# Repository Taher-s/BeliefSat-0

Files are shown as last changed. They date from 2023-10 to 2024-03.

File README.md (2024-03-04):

# BeliefSat-0

BeliefSat-0 is developed by students of K.J. Somaiya Institute of Technology to widen the reach of Amateur Radio-operators around the globe. The payload is a part of tribute to 100 years of Amateur Radio in India and meant to be in service to the Amateur radio community worldwide. The payload performs UHF to VHF FM Voice Repeating and APRS Digipeating. It has the following amateur radio payloads onboard:

1. Amateur Band UHF to VHF FM voice repeater with 12.5 KHz max bandwidth and 12.5 KHz channel spacing. 67.0 Hz CTCSS tone for uplink. 
1. VHF APRS Digipeater with 71.9 Hz CTCSS tone on the uplink. 

The project was developed by the dedicated student team of our Institute's Student Satellite Program “New Leap Initiative”, led by the expertise of Principal Investigator Dr. Umesh Shinde. 

This project aims to develop and demonstrate the technology utilizing nano-satellite technology to make space tech more accessible to educational and low budget commercial missions, by utilizing inexpensive, off the shelf technologies and easily available materials. 

Working of BeliefSat-0:

1. The satellite was launched through PSLV, this opportunity was presented to us by IN-SPACe (ISRO) as part of their POEM (PSLV Orbital Experimental Module)
1. The satellite is positioned in a 350km orbit with a 8 to 9-degree inclination.
1. Its major function is voice repeating and APRS digipeating for the HAM radio community.
1. In the final stage of the PSLV, the satellite will have a continuous power supply which ensures the satellite's functionality.

### What is it made of? What does it look like? What are its dimensions and mass?

Structure: 

The external structure is constructed using Aluminum 8011.



Mechanical Interface:

|**ID**|**Parameter**|**Unit**|**Specification**|
| :-: | :-: | :-: | :-: |
|Mechanical||||
|1\.|Maximum Estimate Mass of the payload|g|500  |
|2\.|Payload Volume(Excluding Antenna)|mm <sup>3</sup>| 150x118x34 |
|3\. |Payload Volume (Including Antenna)|mm <sup>3</sup>| 150x118x512|
|4\.|Antenna Length (Nagoya NL-770S VHF/UHF High Gain Mobile Antenna)|mm|480|
|5\.|Payload mechanical interface||6x M5 HEX steel bolt|

# How is it Powered?

**Electrical interface:**

Power for the payload is supplied from the launch vehicle to which it is connected by a DB9 connector.

The interface connector details are provided in the table given below:

|**CONNECTOR TYPE**|D-sub 9 Pin Connector|
| :- | :- |
|**On payload**|RECEPTACLE-TYPE (female) (Refer **Images** for pictorial information)|
|**On Launch Vehicle**|PIN-TYPE (male)|
|**Location**|On the side plate, which is situated in the XZ plane (along negative Y axis)|

Only the VCC and the ground pin of the DB9 connector are connected to the vehicle.

Power requirements:

Our payload requires a nominal power supply of 2W and peak power supply of upto 10W

# How does it communicate?

**Transciever Specs**

**VHF**
-**Name :** [DRA818V](http://www.dorji.com/products.php?Keyword=dra818v)
-**Frequency Range :** 134~174 Mhz
-**Channel Space :** 12.5/25 KHz
-**TX Current :** 450/750 mA
-**Temperature :** -20°C ~ +70°C
-**Output Power :** +27/30 dbm
-**Reciever Sensitivity :** -122 dbm (As per datasheet, observed sensititvity yet to be calculated)
 
**UHF**
-**Name :** [DRA818U](http://www.dorji.com/products.php?Keyword=dra818u)
-**Frequency Range :** 400~470 Mhz
-**Channel Space :** 25 KHz
-**TX Current :** 450/750 mA
-**Temperature :** -20°C ~ +70°C
-**Output Power :** +27/30 dbm
-**Reciever Sensitivity :** -122 dbm (As per datasheet, observed sensititvity yet to be calculated) (UHF will only be used for voice repeater uplink)

**Antenna:**

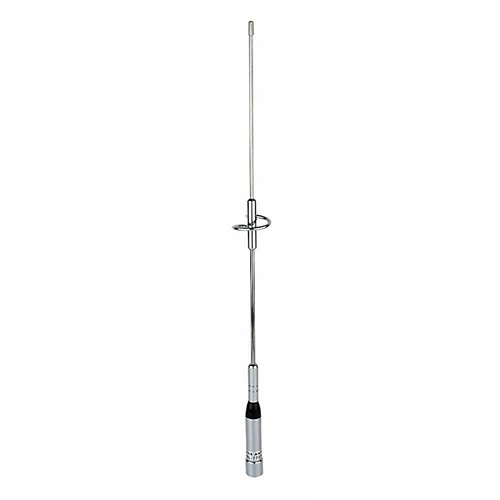
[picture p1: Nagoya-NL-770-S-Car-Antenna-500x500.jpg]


**Nagoya NL-770S VHF/UHF High Gain Mobile Antenna:**

This antenna boasts a unique feature where the satellite's outer cover serves as the grounding mechanism. The carefully engineered radiation pattern, along with impressive gain parameters, ensures strong signal reception and transmission.

What sets the NL-770S apart is its robust construction, making it a reliable choice for various conditions. Its dual-band capabilities cover both VHF and UHF frequencies, enhancing its versatility. The antenna's strategic placement on the satellite, connected via a UHF connector at the top, optimizes signal performance.

**Link Budget:**

- UHF Uplink Budget:

i. Calculation of FSPL() 

= 20x log(D) + 20x log(F) + 20x log (4x pi/c) - G<sub>TX</sub>  - G<sub>RX</sub>               
= 149.9724 dBm

ii. Calculation of Power Received (P<sub>RX</sub>)

= P<sub>TX</sub>+G<sub>TX</sub>-L<sub>TX</sub>-L<sub>FSPL</sub> -L<sub>RX</sub> +G<sub>RX</sub> -</sub> L<sub>M</sub>
= 46.99 + 0 - 0 - 149.9724 - 0 + 0 - 0
= -102.9824 dBm

iii. Link Margin

= P<sub>RX</sub> - RS (Receive Sensitivity)
= (-102.9824 ) - (-122 )
= 19.0176 dBm

- VHF Uplink Budget:

i. Calculation of FSPL

= 20x log(D) + 20x log(F) + 20x log (4x pi/c) - G<sub>TX</sub>  - G<sub>RX</sub>               
= 140.4300 dBm

ii. Calculation of Power Received (P<sub>RX</sub>)

= P<sub>TX</sub>+G<sub>TX</sub>-L<sub>TX</sub>-L<sub>FSPL</sub> -L<sub>RX</sub> +G<sub>RX</sub> -</sub> L<sub>M</sub>
= 46.99 + 0 - 0 - 140.4300 - 0 + 0 - 0
= -93.44 dBm

iii. Link Margin

= P<sub>RX</sub> - RS (Receive Sensitivity)
= (-93.44 ) - (-122 )
= 28.56 dBm

- VHF Downlink Budget:

i. Calculation of FSPL

= 20x log(D) + 20x log(F) + 20x log (4x pi/c) - G<sub>TX</sub>  - G<sub>RX</sub>               
= 140.4300 dBm

ii. Calculation of Power Received (P<sub>RX</sub>)

= P<sub>TX</sub>+G<sub>TX</sub>-L<sub>TX</sub>-L<sub>FSPL</sub> -L<sub>RX</sub> +G<sub>RX</sub> -</sub> L<sub>M</sub>
= 30 + 0 - 0 - 140.4300 - 0 + 0 - 0
= -110.43 dBm

iii. Link Margin 

= P<sub>RX</sub> - RS (Receive Sensitivity)
= (-110.43) - (-121.88 )
= 11.45 dBm

**Operational Modes:**

The operational modes of the payload are:

1. Safe mode (initial mode) : Telemetry once every 30 seconds
1. Digipeater only mode :Telemetry once every 60 seconds and digipeater functionality active
1. Full function mode : Telemetry once every 60 seconds, both digipeater and voice repeater active

In the following description, we have listed three different commands:

1\. Command: !MODE\_CHANGER@<ModeNumber>

Description: This command is used to change the operating mode, and it accepts a ModeNumber parameter that can be set to 0, 1, or 2. Essentially, 0,1, or 2 corresponds to modes 1,2 and 3. 

2\. Command: !VHF\_RX\_FREQ\_CHANGER #<FREQUENCY>

Description: This command is employed for altering the receiving (RX) frequency of a VHF (Very High Frequency) device. You need to specify the desired frequency using the FREQUENCY parameter.

3\.Command:  !VHF\_TX\_FREQ\_CHANGER %<FREQUENCY>

Description: This command allows you to modify the transmitting (TX) frequency of a VHF (Very High Frequency) device. To do this, provide the new frequency as the FREQUENCY parameter.

**Satellite Mode Sequencing and Safety Protocols:**
Upon satellite power-up, it initiates in safe mode, consistently transmitting telemetry every 30 seconds. Following a day of safe mode operations, we issue a command to transition to the digipeater mode. Subsequently, we maintain a one-day duration in digipeater mode before issuing a command to switch to the full mode, enabling both repeater and digipeater functionalities.

The satellite remains in this state, with a daily reset counter uplink command to sustain control. If the reset counter command is not received on any day, it indicates a receiver fault or operational issue. Consequently, the satellite autonomously reverts to safe mode until receiving reactivation instructions, a measure to mitigate potential spurious emissions in cases where the transmitter malfunctions and communication cannot be established.

Hence, a daily connection is imperative, ensuring full communication; otherwise, only telemetry will be transmitted, maintaining the satellite in a state similar to a sputnik.

**What are the different packet types and packet formats?**

**Telemetry Packet**

APRS TELEMETRY FORMAT : The on-air packet telemetry format is as follows:

------>t#51,0,255,255,-12.40,-12.40,xxxxxxBeliefSat<------

51 : LSB of total number of system resets.

0 : MSB of total number of system resets.

255: LSB of total number of resets induced by watchdog

255 : MSB of total number of resets induced by watchdog

-12.40: Temperature sensor 1 reading (Temperature of  Payload )

-12.40: Temperature sensor 2 reading (Temperature of Transreceiver)

xxxxxx : Used as a separation for easier extraction of data in json format

BeliefSat: Name of our Satellite BeliefSat0

References for converting Sensor data into readable format
1. NTC Thermistor: https://robu.in/wp-content/uploads/2016/03/NTC-datasheet.pdf

Refrences for power IC is given below:
1. DC/DC Convertor: https://drive.google.com/drive/folders/0AMwc4gtF42UDUk9PVA

Reference for transreceivers

1. DRA818V :-  [Datasheet](http://www.dorji.com/docs/data/DRA818V.pdf)
1. DRA818U :-  [Datasheet](http://www.dorji.com/docs/data/DRA818U.pdf)

The implementation of APRS packeting system for this project is largely credited to Github user markqvist's LibAPRS repository(https://github.com/markqvist/LibAPRS.git)

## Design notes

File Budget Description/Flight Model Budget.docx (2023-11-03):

To complete the Flight model, following are the expenses towards it:

1. | PCB design and Assembly | Rs. 40000/-
2. | Launch Agreement (Request mail sent to ISRO for concession in launch amount) | Rs. 210000/-
3. | Environmental Testing at SAMEER Kharghar (Request mail sent by PROVOST Sir to DG, SAMEER to reduce the testing cost) | Rs. 332000/-
4. | Traveling for testing and Flight model Submission at SHAR | Rs. 50000/-
| Total | Rs. 632000/-

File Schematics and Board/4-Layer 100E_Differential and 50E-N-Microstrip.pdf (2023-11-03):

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
790 | 50 | 70 | 90 | 110 | 130 | 150 | 170 | 190 | 210 | 230 | 250 | 270 | 290 | 310 | 330 | 350 | 370 | 390 | 410 | 430 | 450 | 470 | 490 | 510 | 530 | 550 | 570 | 590 | 610 | 630 | 650 | 670 | 690 | 710 | 730 | 750 | 770 | 790 | 810 | 830 | 850 | 870 | 890 | 910 | 930 | 950 | 970 | 990 | 1010 | 1030
StackName: 2-Layer | Version: | Revision: | Modification: | Date of Revision: | Editor | Page 2/2
Date: 11-02-2023 | Associated Documents:
Author:
Department:
Site:

www.polarinstruments.com

| Polar Samples | ID/001 | Screened Ident
Polar Samples | SM/001 | Liquid PhotoImageable Mask | 4.000
1 | Polar Samples | FO/002 | Copper Foil | 1.378 | 1, 2, 3
Polar Samples | PP/004 | PrePreg 1651 | 5.906 | 4.200
2 1.378
ISOLA | FR4 | FR4 | 47.244 | 4.300
3 1.378
Polar Samples | PP/004 | PrePreg 1651 | 5.906 | 4.200
4 | Polar Samples | FO/002 | Copper Foil | 1.378 | 4, 5
Polar Samples | SM/001 | Liquid PhotoImageable Mask | 4.000
Polar Samples | ID/001 | Screened Ident ⁶⁴.5669
1 | Coated Microstrip 1B | 1 | 2 | 0 | 9.700 | 0.000 | 49.840 | 50.000 | 10.000 | 0.000
2 | Coated Coplanar Strips With Lower Ground 1B | 1 | 2 | 0 | 8.800 | 0.000 | 50.330 | 50.000 | 10.000 | 9.000
3 | Coated Coplanar Strips With Lower Ground 1B | 1 | 2 | 0 | 8.600 | 0.000 | 50.180 | 50.000 | 10.000 | 8.000
4 | Coated Microstrip 1B | 4 | 3 | 0 | 9.700 | 0.000 | 49.840 | 50.000 | 10.000 | 0.000
5 | Coated Coplanar Strips With Lower Ground 1B | 4 | 3 | 0 | 8.800 | 0.000 | 50.330 | 50.000 | 10.000 | 9.000

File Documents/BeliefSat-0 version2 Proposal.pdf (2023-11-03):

Name of the hosted payload: BeliefSat-0

A. Detailed description of Payload
a) Objective & Introduction
In the rapidly advancing field of space technology, ease of access has frequently posed a challenge, placing restrictions on educational and commercial ventures with limited funding. The proposed project, titled "BeliefSat-0," represents an inspired effort that aims to ignite student curiosity and engagement in the domains of radio-frequency communication and space technology. This project is set to serve as a driving force for STEM education, paving the way for fresh perspectives and involvement.

BeliefSat-0 is developed by students of K.J. Somaiya Institute of Technology to widen the reach of Amateur Radio-operators around the globe. The payload is a part of tribute to 100 years of Amateur Radio in India and meant to be in service to the Amateur radio community worldwide. The payload will perform UHF to VHF FM Voice Repeating and APRS Digipeating. It will have the following amateur radio payloads onboard:

1. Amateur Band UHF to VHF FM voice repeater with 2.5 KHz max bandwidth and 12.5 KHz channel spacing. 67.0 Hz CTCSS tone for uplink.
2. VHF APRS Digipeater with 71.9 Hz CTCSS tone on the uplink.

The ongoing project is in an advanced stage of development by the dedicated student team of our Institute's Student Satellite Program “New Leap Initiative”, led by the expertise of Principal Investigator Dr. Umesh Shinde. At present, significant progress has been made, with the engineering model fully developed and the project now entering the rigorous testing phase. The consistent support from the Institute, serving as the primary funding entity, has played a pivotal role in ensuring the project's continuous advancement, with allocated R&D funds providing vital resources as needed.The team also has got support from the Nanoscience centre of the University of Mumbai for use of cleanrooms, vacuum chambers.

The Principal Investigator has prior experience of creating a Conceptual design of the mission to Jupiter’s moon during “Touch the Jovian Moon: Lander Mission Design Contest” organised by LPSC-ISRO in which they have been winners. The team also has worked on the development of Radiosondes for an Indigenous Upper-Air Sounding System being developed by K.J.S.I.T. in collaboration with DataByte Services and Systems under Make in India initiative. The principal investigator (VU3CDI) is a licensed Amateur Radio Operator. Additionally, the CROWN committee at its core, champions Amateur Radio by sharing essential knowledge and skills. Educational classes equip enthusiasts, including active students, for success in this field. Fostering unity and collaboration among members, especially students, leads to a vibrant exchange of insights and support. This collective effort drives the growth and innovation of the Amateur Radio community. Team has, in the past been successful in developing antennas and software setup for tracking NOAA, METEOR and ISS- ARISS-SSTV downlinks.

b) Payload Objectives :

### 1. Broad Objective:

The proposed project aims to develop and demonstrate the technology utilizing nano-satellite technology to make space-tech more accessible to educational and low budget commercial missions, by utilizing inexpensive, off the shelf technologies and easily available materials.

### 2. Technical Objective:

i. To design the telemetry downlink in such a way that students of different institutes could use inexpensive software-defined radios to receive it with minimal setup, thus giving fuel to curiosity and liking towards STEM education.

ii. To give the ability to the global amateur radio community to use the on-board UHF to VHF FM Voice Repeating and APRS Digipeating for QSOs using inexpensive handy radio setups. (In this case, Baofeng UV-5R being one of the cheapest and most popular handy radios among beginner amateur community, was targeted). This objective has a social and educational objective of getting more students and the general public involved in amateur radio hobby, by giving them an inexpensive access to space-based communication.
iii. To design FSK repeater capabilities in such a way that those could be accessible by off-the-shelf FSK modules available for general IoT projects as well as SDRs like RTL-SDR.
c) Payload specifications

The specifications of the proposed project have been shown in Table below.

1. Specifications of the Payload:
Maximum Estimate Mass of the payload | 500 g
Payload Dimensions (Including Antenna) | Approx. 150x118x512 mm ³
Electrical Interface | On Payload: M24308/23-25F D-Sub Mil Spec Connectors R/A RCP ASSY 9 POS SER 109 From Platform: The expected connection is a male DB9 D-sub connector (9 Pin ) with locking screws on the platform, like a VGA cable
Power requirement from PS4-OP | 28V(raw) for entire duration
Antenna | Nagoya NL-770S VHF/UHF High Gain Mobile Antenna
Participation in integration | Principal Investigator with 2 students will participate.

Post Launch requirements | Tracking and TLE of BeliefSat-0
Command and control station location | KJSIT
Call-sign of the station operator | VU3CDI

Table 1: Specifications of Proposed Payload

2. Payload Description:
BeliefSat-0 is developed by students of K.J. Somaiya Institute of Technology to widen the reach of Amateur Radio-operators around the globe. The payload is a part of tribute to 100 years of Amateur Radio in India and meant to be in service to the Amateur radio community worldwide. The payload will perform UHF to VHF FM Voice Repeating and APRS Digipeating.

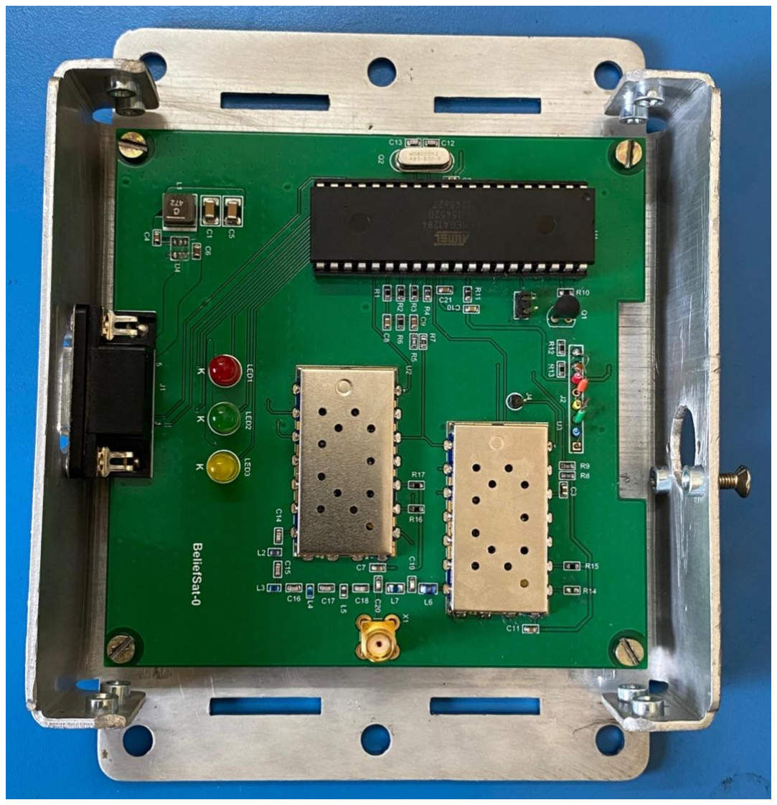
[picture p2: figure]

Fig 2: The engineering model of BeliefSat-0

i. Antenna:

Nagoya NL-770S VHF/UHF High Gain Mobile Antenna:

This antenna boasts a unique feature where the satellite's outer cover serves as the grounding mechanism. The carefully engineered radiation pattern, along with impressive gain parameters, ensures strong signal reception and transmission.

What sets the NL-770S apart is its robust construction, making it a reliable choice for various conditions. Its dual-band capabilities cover both VHF and UHF frequencies, enhancing its versatility. The antenna's strategic placement on the satellite, connected via a UHF connector at the top, optimizes signal performance.

ii) Structure:
Given below is the structural design of our payload with dimensions:

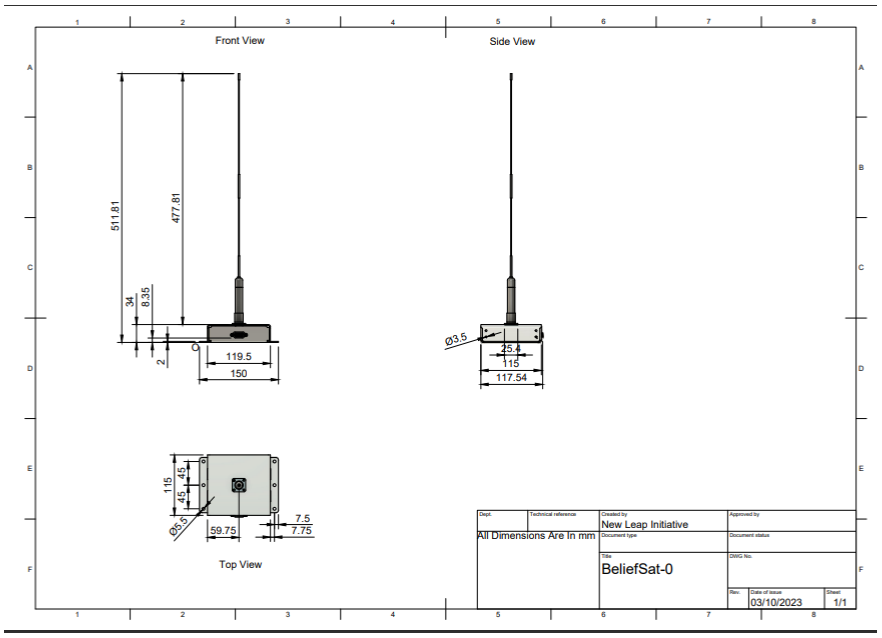
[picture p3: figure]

iii) Electrical Interface:

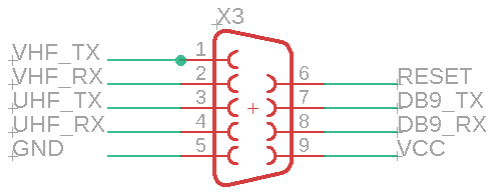
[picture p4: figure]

CONNECTOR TYPE | D-sub 9 Pin Connector
On BeliefSat-0 | RECEPTACLE-TYPE (female)
On Launch Vehicle | PIN-TYPE (male)
iv) | Microcontroller:

ATmega328P is the microcontroller used. The ATmega series is developed by Microchip Technology (formerly Atmel Corporation) is part of the AVR microcontroller family and offers a range of features suitable for various applications, including embedded systems, robotics, and electronics projects. With its advanced capabilities and generous memory, the ATmega328P is well-suited for complex tasks that require efficient processing and control. The selected microcontroller has peripherals like SPI, I2C, Serial, which makes it compatible with most modules in the market. Additionally, it can be easily programmed using Arduino IDE.

v) UHF/VHF Voice Repeater:
An innovative crossband repeater strategy involves pairing VHF and UHF DRA818 transceivers. This dynamic setup enables the seamless rebroadcasting of FM-modulated voice or APRS signals from an input UHF frequency to an output VHF frequency. Emitting at 0.5W output power, the signal remains accessible even to basic walkie talkies. The exceptional input sensitivity of -122dBm ensures quick activation, triggered by the standard 4W output power of prevalent terrestrial amateur radio walkie talkies like the Baofeng UV-5R.

vi) FSK Digipeater:
The primary transceiver also boasts an additional capability to adeptly store-and-forward repeater for concise messages of up to 140 characters. This advanced feature relies on FSK modules, enabling the transceiver to adeptly process and relay brief messages sent its way.

vii) Link Budget:
- UHF Uplink Budget:
i. Calculation of FSPL() = 20x log(D) + 20x log(F) + 20x log (4x pi/c) - GTX - GRX = 149.9724 dBm

ii. Calculation of Power Received (PRX) =PTX+GTX-LTX-LFSPL -LRX +GRX -LM =46.99 + 0 - 0 - 149.9724 - 0 + 0 - 0 = -102.9824 dBm

iii. Link Margin = PRX - RS (Receive Sensitivity)
= (-102.9824 ) - (-122 )
= 19.0176 dBm
- VHF Uplink Budget:
i. Calculation of FSPL = 20x log(D) + 20x log(F) + 20x log (4x pi/c) - GTX - GRX = 140.4300 dBm

ii. Calculation of Power Received (PRX) =PTX+GTX-LTX-LFSPL -LRX +GRX -LM =46.99 + 0 - 0 - 140.4300 - 0 + 0 - 0 = -93.44 dBm iii. Link Margin = PRX - RS (Receive Sensitivity) = (-93.44 ) - (-122 )
= 28.56 dBm
- VHF Downlink Budget:
i. Calculation of FSPL = 20x log(D) + 20x log(F) + 20x log (4x pi/c) - GTX - GRX = 140.4300 dBm

ii. Calculation of Power Received (PRX) = PTX+GTX-LTX-LFSPL -LRX +GRX -LM
=30 + 0 - 0 - 140.4300 - 0 + 0 - 0 = -110.43 dBm

iii. Link Margin = PRX - RS (Receive Sensitivity)
= (-110.43) - (-121.88 )
= 11.45 dBm
c) Specific requirements from POEM (Stability, pointing, orbit type, power etc.) and constraints on payload operation (Electrical, mechanical, environmental)
1. We require 28V(raw) power for the entire duration via male DB9 Connector.
2. Stabilized platform not required
d) Plans for data processing, management and archival
The telemetry and the packets reflected by the digipeater will be received by indigenous ground-stations at K. J. Somaiya Institute of Technology (KJSIT) and will be stored in a local database.
e) Definition of success criteria of the payload

The successful operation of the payload is voice repeating, APRS digipeating functions and changing through different modes of operation using commands sent from the ground station.

B. Development strategy
T0 | Present | 1. Prototype fabrication completed
T0 + 5 weeks | In-house functional testing with firmware | 1. Functional testing of prototype 2. Application for ITU and IARU frequency coordination 3. Designing firmware
T0 + 6 weeks | RF output sensitivity and testing using spectrum analyser | 1. RF output sensitivity and testing using spectrum analyser 2. In-house RF output and Power generation functional testing.
T0 + 7 weeks | Functional testing at Nano-science centre | 1. Preliminary thermal-vacuum bakeout after integration with the satellite at Nanoscience centre University of Mumbai.
T0 + 9 weeks | Flight model fabrication & testing | 1. Fabrication of the flight model (if necessary) 2. Assembly of flight model in clean-room
T0 + 10 weeks | Testing payload using in-house ground station | 1. Testing payload using in-house ground station
T0 + 12 weeks | Qualification Testing | 1. Performing all the required tests like environmental testing, themovac testing, vibration testing and other necessary standard tests.
T0 + 13 weeks | Submission of payload and all the relevant documentation to ISRO | 1. Documentation of code, designs and final test procedures and finalization of required permissions and documents.

C. In case POEM communication capabilities are not required
The team plans to set up its own indigenous ground station at KJ Somaiya Institute of Technology (KJSIT), Sion Mumbai. KJSIT hosts its own Amateur Radio Club – CROWN (Club of Radio Operations and Wireless Networks, VU2CWN) which is a registered club under Wireless Planning and Communication (WPC) wing of Department Of Telecommunication (DOT).
The location of the institute is:
KJ Somaiya Institute of Technology, Sion Mumbai
Somaiya Ayurvihar Complex, Eastern Express Highway, Near Everard Nagar, Sion East, Mumbai, Maharashtra 400022.
CROWN (Club of Radio Operations and Wireless Networks, VU2CWN)
Managed by Dr. Umesh Shinde.
Parameter | Value
Max Bandwidth | 2.5 KHz
Modulation | Frequency Shift Keying (FSK)
Uplink Frequency | 437.525 MHz
Downlink Frequency | 145.525 MHz
Channel Spacing | 12.5 KHz

Data Rates in bps

Telemetry Downlink | 1200
Digipeater Downlink | 1200
Command Uplink | 1200
Digipeater Uplink | 1200

CTCSS tone for uplink

Voice Repeater | 67.0 Hz
APRS Digipeater | 71.9 Hz

D. Description of required post-launch ground operation support.
a. Coordinates of payload.
b. Initial TLEs for the deployed satellite to be provided by the launch service provider.
E. Expected cost for payload realization and source of funding (Intended end use of the experimental payload)
Fully funded by KJ Somaiya Institute of Technology, Sion Mumbai.

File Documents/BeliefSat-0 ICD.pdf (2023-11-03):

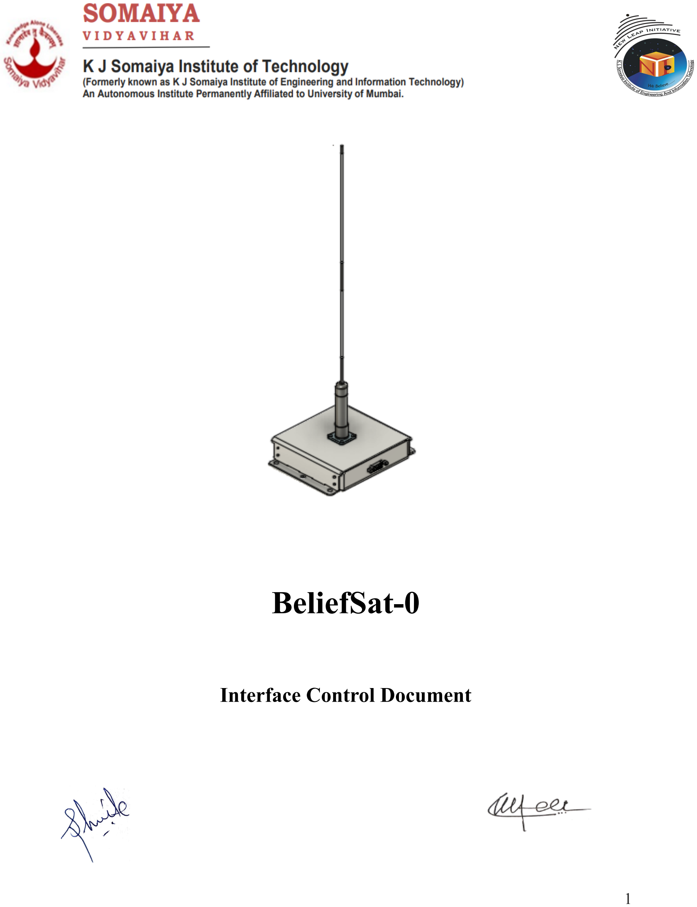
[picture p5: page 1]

# BeliefSat-0

## Interface Control Document

Revised Version | Release Date | Change Record | Effective Pages
1.0 | 25/08/2023 | Proposal Submission | 12
2.0 | 27/09/2023 | Removal of Camera because of tumbling Platform | 12
3.0 | 05/10/2023 | i) Dimensions Changes ii) Addition of Temperature Measure Unit iii) Addition of Short Circuit Protection And Reverse Polarity Protection | 18
4.0 | 18/10/2023 | Change in Fuse | 18
5.0 | 01/11/2023 | Addition of Frequency Band Details in Design Description | 19
6.0 | 02/11/2023 | Typographic mistake in the description of telecommands in Table 1 has been corrected. Frequency Bandwidth changed from 25KHz to 12.5KHz | 19
Revision no. | Approval
Prepared by | Reviewed by | Verified by | Approved by
6.0 | Dhriti Kothari Team Member Student, KJSIT | Sheetal Popat Team Manager Student, KJSIT | Dr. Umesh Shinde Dean, Research Development and Consultancy, KJSIT | Dr. Suresh Ukarande Principal, KJSIT

Sr. no. | CONTENTS | Page No.
1 | Introduction | 5
1.1 | Overview | 5
1.2 | Document Purpose | 5
2 | Payload Overview | 6
2.1 | Design Description | 6
2.2 | General System Requirements | 10
2.3 | Payload Design Parameters | 11
2.4 | Coordinate System | 12
3 | Physical Interfaces | 13
3.1 | Mechanical Interfaces | 13
3.2 | Mass Properties | 14
4 | Electrical Interface | 15
4.1 | Payload - Launch Vehicle Interface | 15

4.2 | The pinouts of DB-9 connector | 15
5 | Appendix A : Overall payload dimensions | 16
6 | Appendix B | 17
7 | Appendix C | 18
8 | References | 19

### 1. Introduction

### 1.1 Overview

BeliefSat-0 is developed by students of K. J. Somaiya Institute of Technology to widen the reach of Amateur Radio-operators around the globe. The payload is a part of tribute to 100 years of Amateur Radio in India and meant to be in service to the Amateur radio community worldwide. The payload will perform UHF to VHF FM Voice Repeating and APRS Digipeating on VHF.

### 1.2 Document Purpose

The interface specifications of Payload are detailed in the document that follows. It provides comprehensive details on the mechanical and electrical interfaces in addition to other important information about the payload.
It will have the following amateur radio payloads onboard:
1. Amateur Band FM voice repeater with 12.5 KHz max bandwidth and 12.5 KHz channel spacing. 67.0 Hz CTCSS tone for uplink.
2. VHF APRS Digipeater with 71.9 Hz CTCSS tone on the uplink.

### 2. Payload Overview

### 2.1 Design Description

Payload is developed by students and the Faculty of K. J. Somaiya Institute of Technology to widen the reach of Amateur Radio-operators around the globe with VHF/UHF FM Voice Repeater and APRS Digipeater.

### 2.1.1 Operational Mode

The operational modes of the payload are:

1. Safe mode (initial mode) : Telemetry once every 30 seconds
2. Digipeater only mode :Telemetry once every 60 seconds and digipeater functionality active
3. Full function mode : Telemetry once every 60 seconds, both digipeater and voice repeater active
Table 1 : Commands for operation mode
Sr. No. | Commands | Description
1. | !MODE_CHANGER@<ModeNumber> | Changes mode between 0,1,2
2. !VHF_RX_FREQ_CHANGER | #<FREQUENCY> | Changes RX frequency of VHF
3. !VHF_TX_FREQ_CHANGER | %<FREQUENCY> | Changes TX frequency of VHF

Note: Detailed command and telemetry formats would be published during frequency coordination

### 2.1.2 Frequency Bands

| VHF Band | UHF Band
Application | Telemetry, Telecommand, Digipeater uplink, Digipeater downlink, Voice Downlink | Voice Uplink
Frequency Range | 144-146 MHz | 435-438 MHz
Desired Central Frequency | 144.2500 MHz | 437.0000 MHz
Bandwidth | 12.5 KHz | 12.5 KHz
Modulation | FM and AFSK over FM | FM
Encoding | APRS over AX.25 using NRZI line coding and AFSK digital Modulation | No Encoding
Transmitting Power | 1W | No Transmit only receive
Area of Operation | Global | Global
Special consideration: | | 3 * VHF Frequency - UHF Frequency | >= 1.5 MHz to prevent feedback loop

### 2.1.3 RF Duplexer Design

Payload has two filter circuits which are HPF (high pass filter) and LPF (low pass filter).
1. High Pass Filter (HPF): This filter allows UHF signals to pass through while blocking VHF signals. By placing an HPF between the DRA818U transceiver and the antenna, it isolates the UHF signals associated with this transceiver from the other.

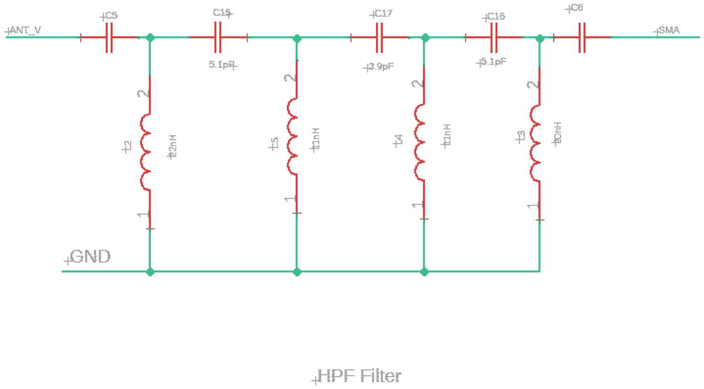
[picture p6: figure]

Fig. 1:High Pass Filter (HPF)
2. Low Pass Filter (LPF): Conversely, an LPF allows VHF signals to pass through while blocking higher-frequency signals. Placing an LPF between the other DRA818 transceiver and the antenna, this helps to isolate the lower-frequency signals associated with that transceiver.

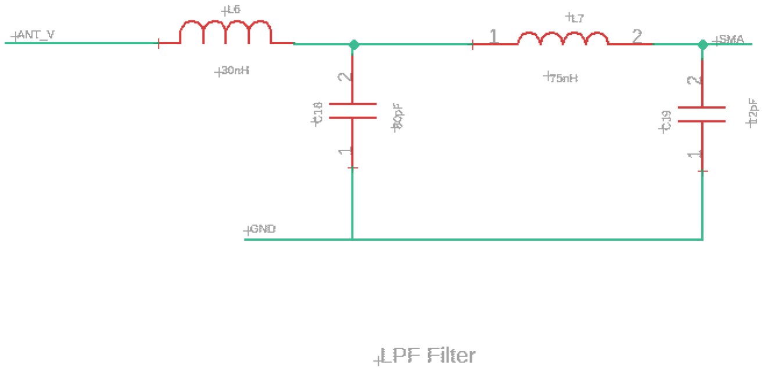
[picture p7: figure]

Fig. 2: Low Pass Filter (LPF)

### 2.1.4 Power Circuit Design:

As per the interface specifications outlined for POEM experimental payloads, the power supplied falls within the range of 24-36 volts in its raw form. To meet these requirements, we have integrated an LM2575S DC to DC buck converter into the system. This converter efficiently transforms the input power into a stable voltage of 3.3 volts while delivering a maximum current output of 2 amperes.

In the implementation of this specific buck converter, two essential protective components have been incorporated. Firstly, a 500mA 125V DC fuse (datasheet included in references) is included to prevent short-circuits effectively. Secondly, a Schottky diode has been employed to ensure reverse polarity protection.
Please refer the provided image below:

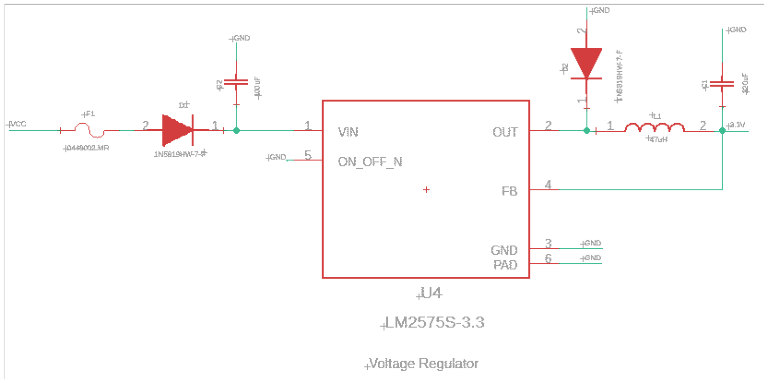
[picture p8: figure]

Fig. 3: Power Circuit Design

### 2.1.5 Temperature measurement unit:

Payload consists of two thermistors (Thermistor 100k NTC) to measure the internal circuit temperature and body temperature. To measure the body temperature one thermistor is fixed to the body using kapton tape and another one fixed on the electronic circuit to measure the circuit temperature.

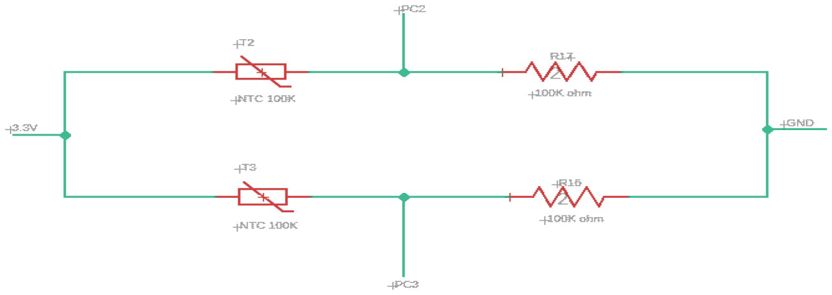
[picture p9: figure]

Fig. 4: Temperature measurement unit

### 2.2 General System Requirements

1. The system includes the necessary electrical and mechanical interfaces with respect to the Launch Vehicle specifications.
2. The payload should be securely connected with the launch vehicle, and is required to receive a continuous power supply within the range of 24V-36V(raw) throughout the entire duration of journey.
3. The payload does not need telemetry and telecommand (TM and TC) requirements from the launch vehicle. Therefore, no communication is required from the platform, except for power supply.

### 2.3 Payload Design Parameters

ID | Parameter | Unit | Specification
| | Mechanical
1. Maximum Estimate Mass of the | payload | g | 500
2. | Payload Volume(Excluding Antenna) | mm ³ | 150x118x34
3. | Payload Volume (Including Antenna) | mm ³ | 150x118x512
4. Antenna Length (Nagoya NL-770S | VHF/UHF High Gain Mobile Antenna) | mm | 480
5. | Payload mechanical interface | | 6x M5 HEX steel bolt

Electrical

6. | Payload electrical interface | - | On Payload: M24308/23-25F D-Sub Mil Spec Connectors R/A RCP ASSY 9 POS SER 109 (Refer Appendix B for pictorial information) From Platform: The expected connection is a male DB9 D-sub connector (9 Pin )
7.. | Power requirement from PS4-OP | - | Nominal: 2 W Peak: 10 W

### 2.4 Coordinate System:

The coordinate system of the payload can be seen in the figure below. The base of the payload is in the XY plane and the antenna is along the Z-axis.

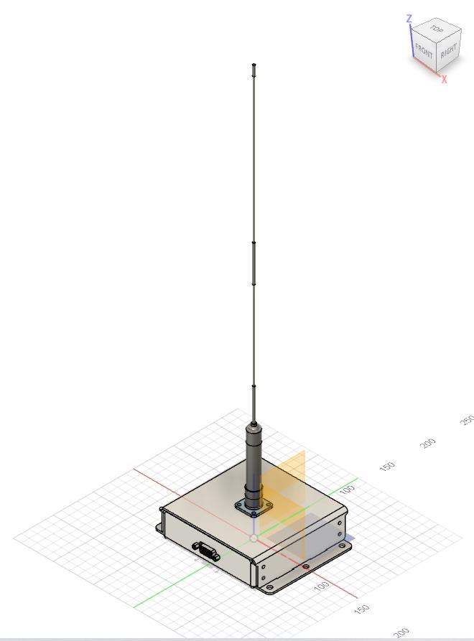
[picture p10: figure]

Fig. 5: Coordinate system

### 3. Physical Interfaces

### 3.1 Mechanical Interfaces

i) The external structure is constructed using Aluminum 8011. The payload is to be mounted on the platform with the help of 6 x M5 HEX steel bolts ( See Fig. 4 ).

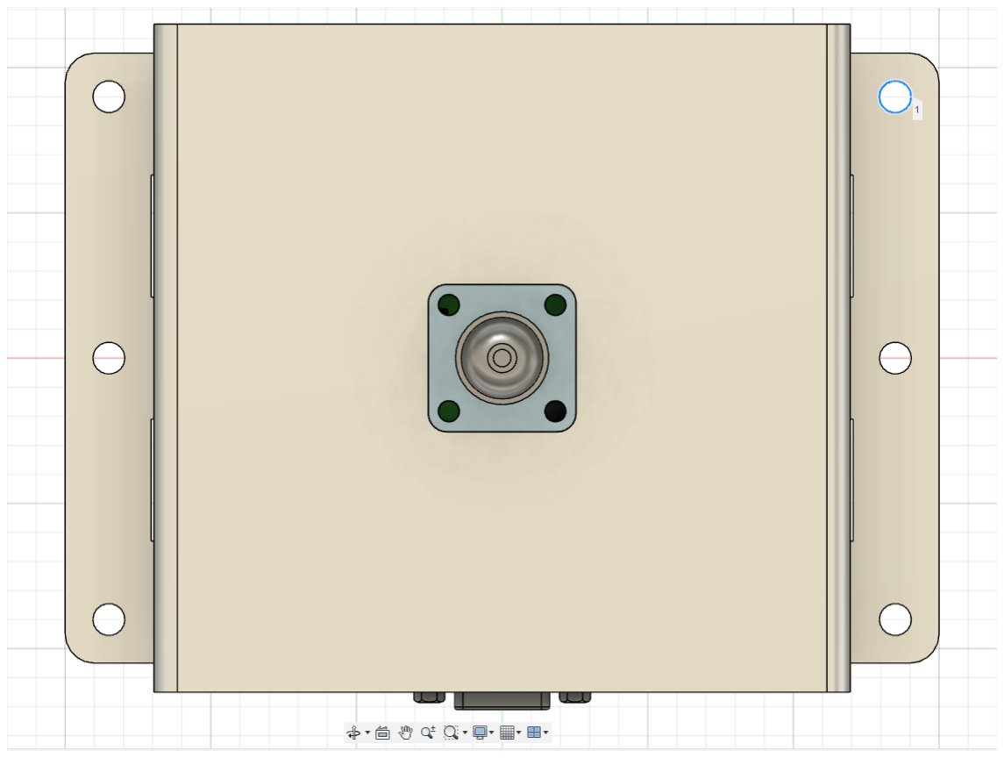
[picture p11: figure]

Fig. 6: 6 M5 holes for mounting
ii) The distance between the center of the mounting hole to the side- wall of the payload is 7.75 mm ( See Fig. 5 ).

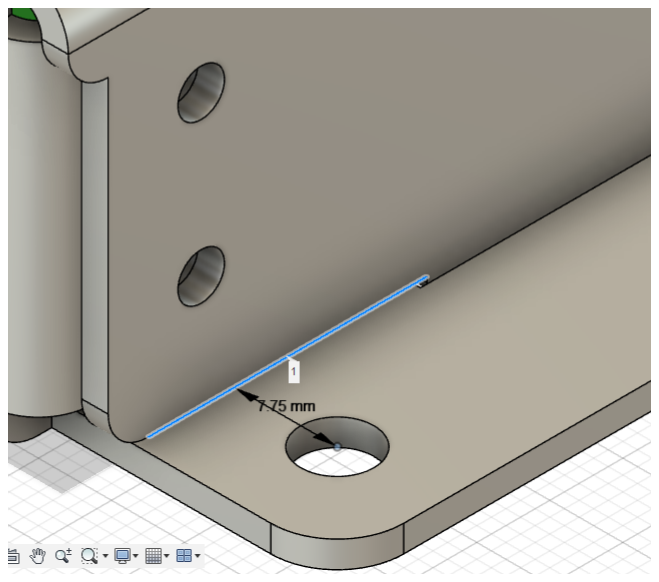
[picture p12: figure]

Fig. 7: Side-wall to mounting hole dimension
iii) Thermal insulating sheet, typically made from material like PEEK, is employed to separate the base from the platform.

### 3.2 Mass properties

Mass, Moment of Inertia and Centre of Mass information is provided in the table below. The values are provided for reference purposes only and it can be used as a baseline input for initial sizing calculations. The following assumptions were taken to generate mass properties:
1. The Moment of Inertia given in the table below is given with respect to the Centre of Mass as well as the Origin position.
Parameter | Value
Mass (g)(Approx.) | 500
Centre of Mass (mm) | X (mm) | -2.324
| Y (mm) | -2.309
| Z (mm) | 27.299
Moment of Inertia (At Centre of Mass) 2 (g mm ) | Ixx | 6 1. 995 x 10
| Iyy | 2.027x 10 6
| Izz | 1. 318 x 10 6
Moment of Inertia (At Origin) 2 (g mm ) | Ixx | 2. 563 x 10 6
| Iyy | 2.595 x 10 6
| Izz | 6 1. 327 x 10

### 4. Electrical Interface

### 4.1 Payload - Launch Vehicle Interface

The interface connector details are provided in the table given below:

CONNECTOR TYPE | D-sub 9 Pin Connector
On payload | RECEPTACLE-TYPE (female) (Refer Appendix B for pictorial information)
On Launch Vehicle | PIN-TYPE (male)
Location | On the side plate, which is situated in the XZ plane (along negative Y axis)

### 4.2. The pinouts of DB-9 connector are given in the table below (we require only VCC

and GND from the platform):

Pin Number | Name | Description
1 | TX_VHF | NC
2 | RX_VHF | NC
3 | TX_UHF | NC
4 | RX_UHF | NC
5 | GND | Ground
6 | RESET_DB9 | NC
7 | TX_DB9 | NC
8 | RX_DB9 | NC
9 | VCC | Power Supply
The schematic diagram of the DB -9 connector is given in Appendix C (Electrical Interface Schematics).

### 5. Appendix A: Overall dimensions of Payload

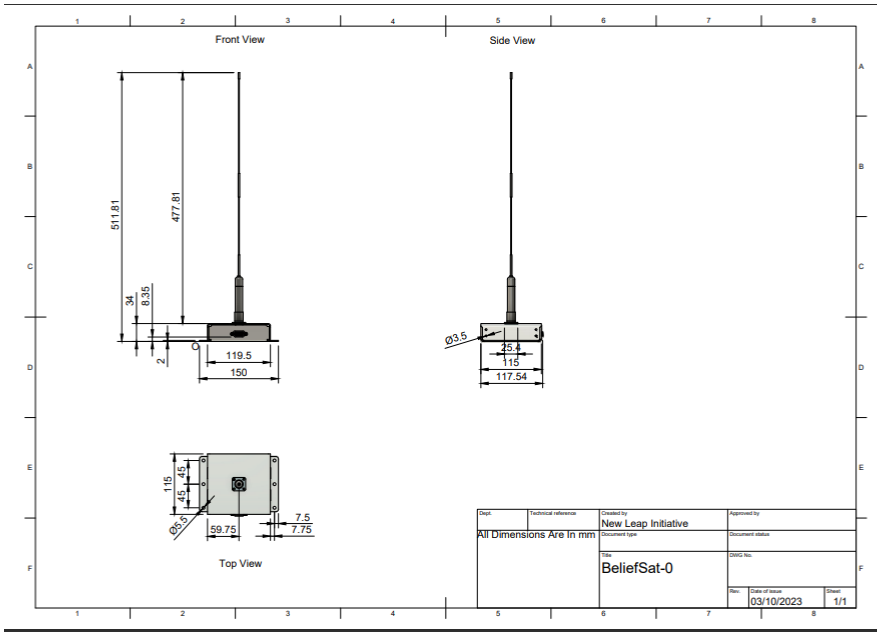
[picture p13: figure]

Fig. 8: Dimensions of Payload (in mm)

### 6. Appendix B: Overall dimensions of Connector Used For Electrical Interface

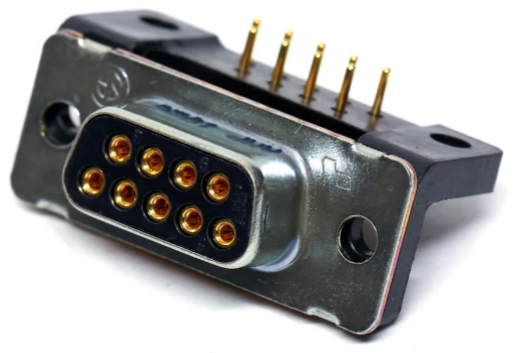
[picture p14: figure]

Fig. 9: M24308/23-25F D-Sub Mil Spec Connectors

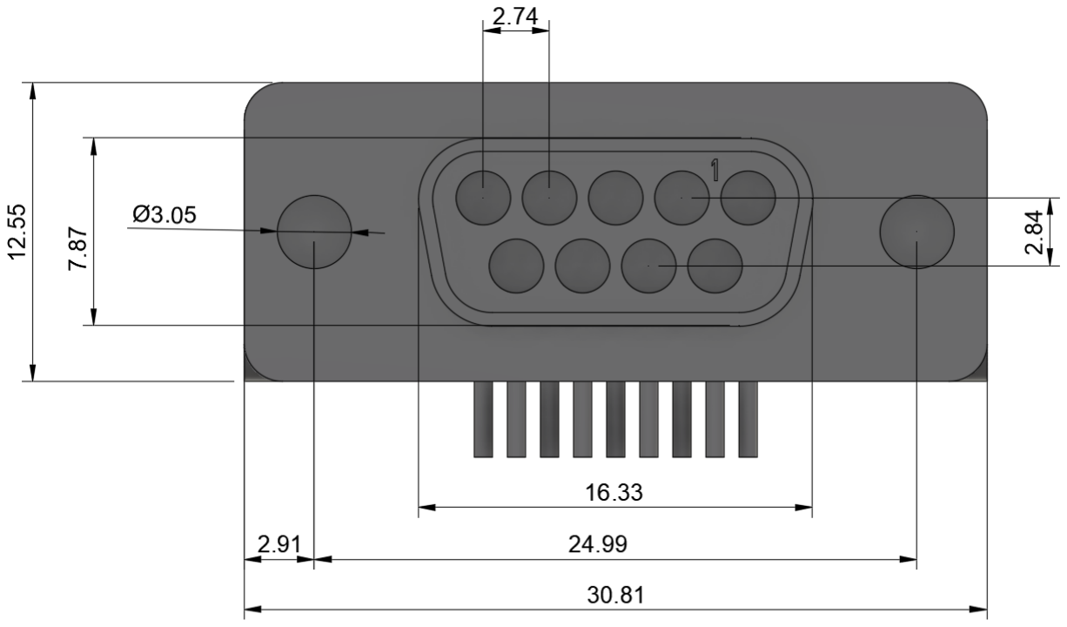
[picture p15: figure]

Fig. 10: DB9 Connector Dimensions
The base of the DB9 connector is positioned at a distance of 10.24 mm above the payload base, while the screws are situated 14.19 mm above the payload base.

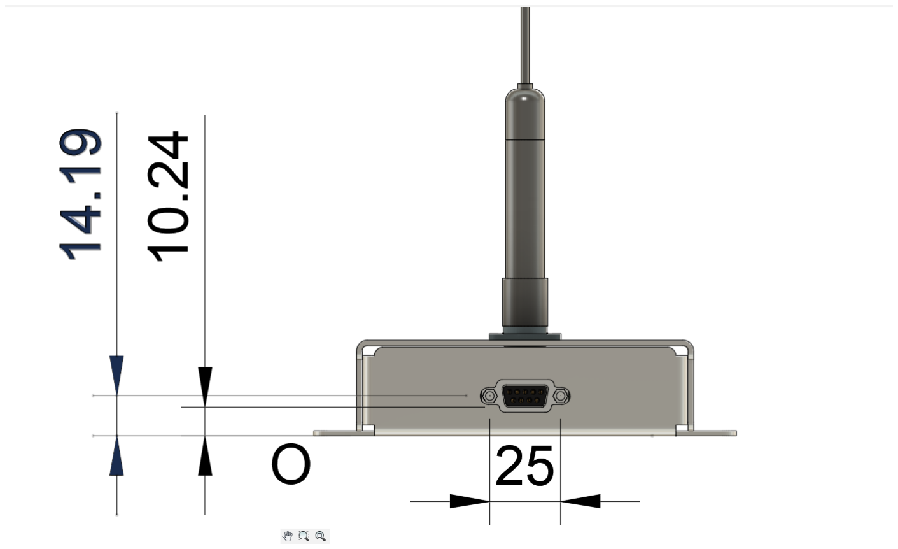
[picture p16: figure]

Fig. 11: DB9 Connector Location on Package

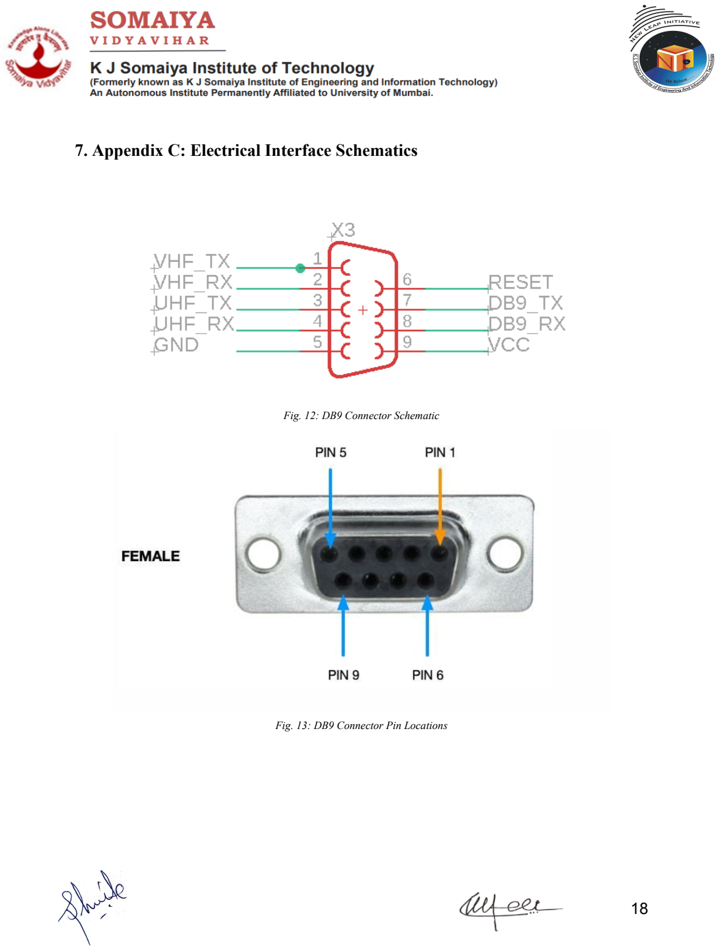
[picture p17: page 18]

### 7. Appendix C: Electrical Interface Schematics

Fig. 12: DB9 Connector Schematic

Fig. 13: DB9 Connector Pin Locations

### 8. References :

i. Microcontroller datasheet (Atmega328P-PU) https://www.mouser.in/datasheet/2/268/ATmega48A_PA_88A_PA_168A_PA_328_P_DS_DS40 002061B-3050139.pdf (https://www.mouser.in/datasheet/2/268/ATmega48A_PA_88A_PA_168A_PA_328_P_DS_DS40002061B-3050139.pdf)

ii. DC to DC Buck Converter (LM2575S IC REG BUCK 3.3V 2A TO263-5L) https://mm.digikey.com/Volume0/opasdata/d220001/medias/docus/5011/LM2575-LM2575HV.p df (https://mm.digikey.com/Volume0/opasdata/d220001/medias/docus/5011/LM2575-LM2575HV.pdf)

iii. Fuse (LITTELFUSE 0451.500MRL) https://drive.google.com/drive/folders/1YPhIgdw0xbcl2YF_EygH_6NI25DQiTfl

iv. Schottky Diode (DIODES INC. 1N5819HW-7-F ) https://in.element14.com/diodes-inc/1n5819hw-7-f/diode-scky-recti-1a-40v-sod123/dp/1773475

v. DB9 connector (M24308/23-25F) https://www.mouser.in/datasheet/2/418/8/TYEL_S_A0000703600_1-2524337.pdf

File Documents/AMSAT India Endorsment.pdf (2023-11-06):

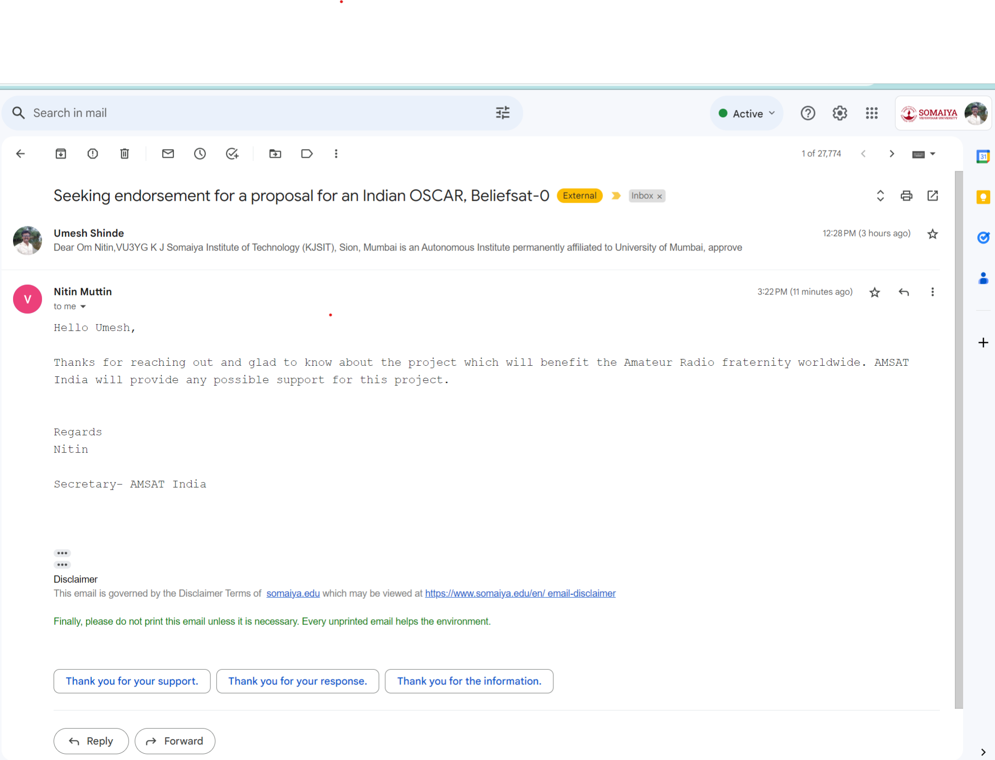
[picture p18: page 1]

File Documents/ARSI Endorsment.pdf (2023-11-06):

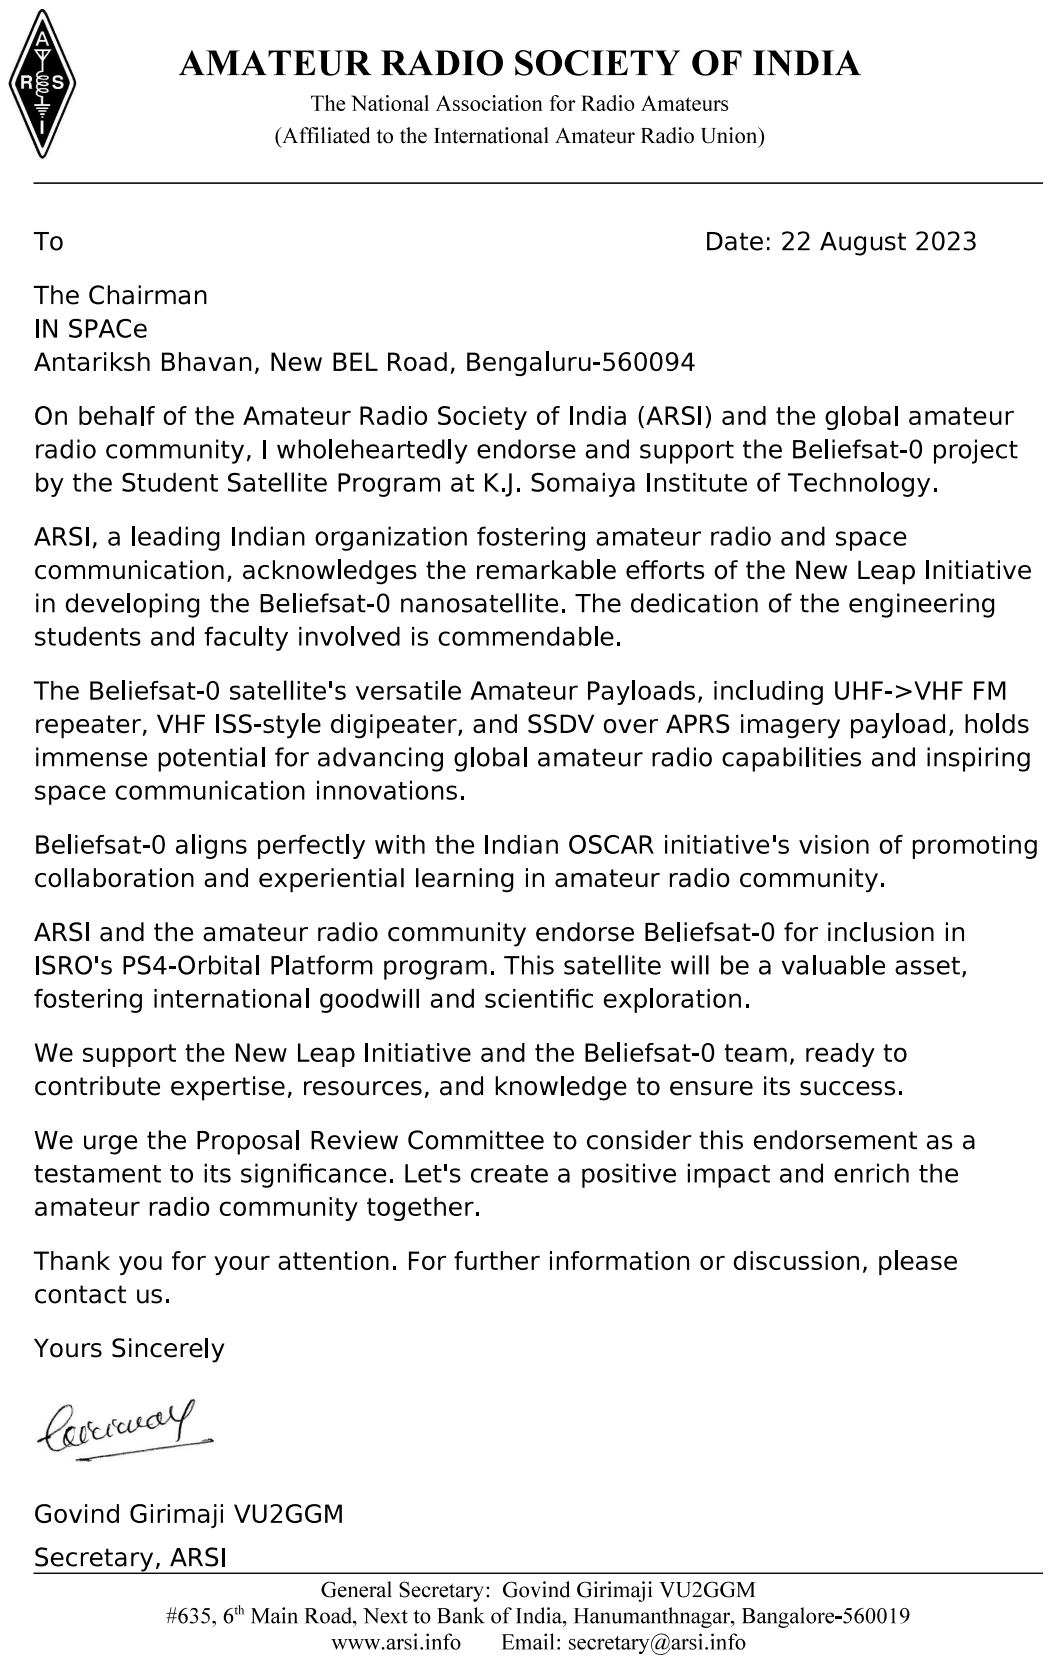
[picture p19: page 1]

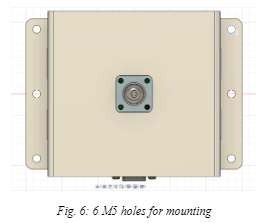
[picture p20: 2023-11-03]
Images/Topview.PNG

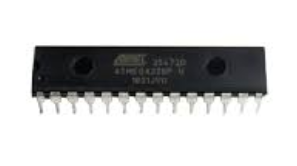
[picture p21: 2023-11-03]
Images/ATmega328P.PNG

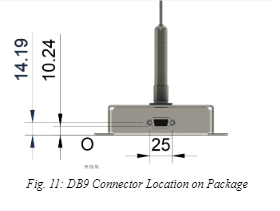
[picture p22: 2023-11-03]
Images/Dimensions of DB9 Connector.PNG

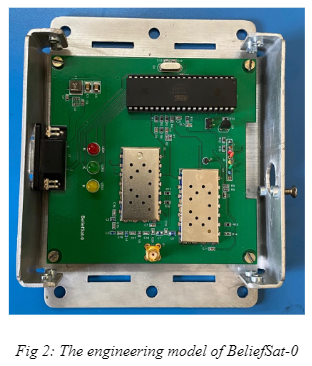
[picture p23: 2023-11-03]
Images/PCB Plate.PNG

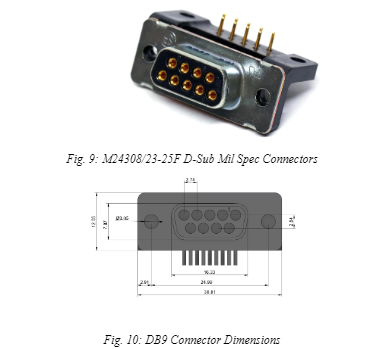
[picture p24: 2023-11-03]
Images/DB9 Connector.PNG

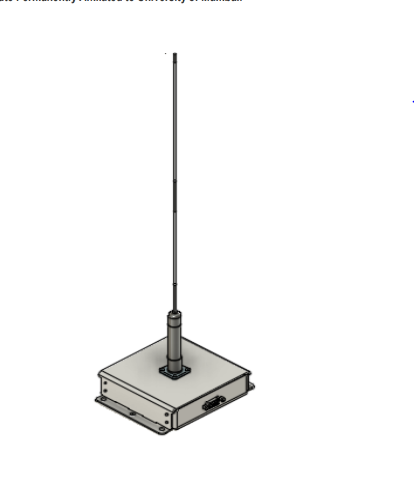
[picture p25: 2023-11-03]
Images/BeliefSat0.PNG

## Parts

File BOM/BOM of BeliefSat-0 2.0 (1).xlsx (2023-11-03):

Sr. No. | Reference Designation | Value | Manufacturer | Manufacturer Part Number | Description | Package | Type
1 | C1 | 100uF | Vishay | 597D107X0035F2T | Surface Mount Tantalum Capacitor, TANTAMOUNT®, 100 µF, 35 V, 3024 [7660 Metric], ± 20%, 0.1 ohm, F | 3024[7660 Metric] | SMD
2 | C2 | 220uF | Murata | GRM31CR60J227ME11L | SMD Multilayer Ceramic Capacitor, 220 µF, 6.3 V, 1206 [3216 Metric], ± 20%, X5R, GRM Series | 1206 [3216 Metric] | SMD
3 | C3,C4,C5,C6 | 22pF | Kemet | C0603C220D5GACTU | MLCC CAPACITOR, 22PF, 50V, C0G, 0.5PF, 0603 | 0603[1608 Metric] | SMD
4 | C7 | 1uF | Kemet | C0603C105K3RACTU | SMD Multilayer Ceramic Capacitor, 1 µF, 25 V, 0603 [1608 Metric], ± 10%, X7R, C Series KEMET | 0603 [1608 Metric] | SMD
5 | C8,C9,C10,C11,C12,C13 | 0.1uF | Kemet | C0603C104J5RACAUTO | SMD Multilayer Ceramic Capacitor, AEC-Q200, 0.1 µF, 50 V, 0603 [1608 Metric], ± 5%, X7R | 0603[1608 Metric] | SMD
6 | C14 | 4.7uF | Murata | GRM188R61E475KE11D | SMD Multilayer Ceramic Capacitor, 4.7 µF, 25 V, 0603 [1608 Metric], ± 10%, X5R, GRM Series | 0603[1608 Metric] | SMD
7 | C15,C16 | 5.1pF | Kemet | CBR06C519B5GAC | Capacitor, RF, C0G / NP0, 5.1 pF, 50 V, HiQ-CBR Series, ± 0.1pF, 125 °C, 0603 [1608 Metric] | 0603[1608 Metric] | SMD
8 | C17 | 3.9pF | Kemet | CBR06C399BAGAC | Capacitor, RF, C0G / NP0, 3.9 pF, 250 V, HiQ-CBR Series, ± 0.1pF, 125 °C, 0603 [1608 Metric] | 0603[1608 Metric] | SMD
9 | C18 | 30pF | Multicomp Pro | MC0603N300J500CT | SMD Multilayer Ceramic Capacitor, 30 pF, 50 V, 0603 [1608 Metric], ± 5%, C0G / NP0, MC | 0603[1608 Metric] | SMD
10 | C19 | 12pF | Yageo | CC0603JRNPO9BN120 | SMD Multilayer Ceramic Capacitor, 12 pF, 50 V, 0603 [1608 Metric], ± 5%, C0G / NP0, CC Series | 0603{1608 Metric] | SMD
11 | L1 | 47uH | Wurth Elektronik | 784777470 | Power Inductor (SMD), AEC-Q200, 47 µH, 1.15 A, Shielded, 1.25 A, WE-PDA | _ | SMD
12 | L2 | 22nH | Coilcraft | 0603CS-22NXGLU | Wirewound Inductor, 22 nH, 0.19 ohm, 3 GHz, 700 mA, 0603 [1608 Metric], 0603CS Series | 0603[1608 Metric] | SMD
13 | L3 | 20nH | Coilcraft | 0603CT-20NXJLU | Wirewound Inductor, 20 nH, 0.175 ohm, 760 mA, 0603 [1608 Metric], 0603CT Series | 0603[1608 Metric] | SMD
14 | L4,L5 | 11nH | Murata | LQW18AS11NG0CD | Wirewound Inductor, 11 nH, 0.086 ohm, 4 GHz, 700 mA, 0603 [1608 Metric], LQW18AS_0C | 0603[1608 Metric] | SMD
15 | L6 | 30nH | Coilcraft | 0805HQ-30NXGLC | Wirewound Inductor, 30 nH, 0.095 ohm, 1.95 GHz, 1.2 A, 0805 [2012 Metric], 0805HQ Series | 0805[2012 Metric] | SMD
16 | L7 | 75nH | Coilcraft | 0603DC-75NXJRW | Wirewound Inductor, AEC-Q200, 75 nH, 0.396 ohm, 1.6 GHz, 860 mA, 0603 [1608 Metric], 0603DC Series | 0603[1608 Metric] | SMD
17 | R1,R2,R3,R4,R5,R15,R18 | 10kΩ | Vishay | CRCW060310K0FKEA | SMD Chip Resistor, 10 kohm, ± 1%, 100 mW, 0603 [1608 Metric], Thick Film, General Purpose | 0603 [1608 Metric] | SMD
18 | R6 | 4.7kΩ | Vishay | CRCW06034K70FKEA | SMD Chip Resistor, 4.7 kohm, ± 1%, 100 mW, 0603 [1608 Metric], Thick Film, General Purpose | 0603 [1608 Metric] | SMD
19 | R7,R8 | 1kΩ | Vishay | CRCW06031K00FKEAHP | RES, THICK FILM, 1K, 1%, 0.25W, 0603 | 0603 [1608 Metric] | SMD
20 | R9,R10,R11,R16,R17 | 100kΩ | Vishay | CRCW0603100KFKEA | SMD Chip Resistor, 100 kohm, ± 1%, 100 mW, 0603 [1608 Metric], Thick Film, General Purpose | 0603[1608 Metric] | SMD
21 | R12 | 270Ω | Vishay | CRCW0603270RFKEA | SMD Chip Resistor, 270 ohm, ± 1%, 100 mW, 0603 [1608 Metric], Thick Film, General Purpose | 0603[1608 Metric] | SMD
22 | R13 | 2.2kΩ | Vishay | CRCW06032K20JNEAHP | RES, AEC-Q200, THICK FILM, 2K2, 333.3mW, ± 5%, 0603 | 0603 [1608 Metric] | SMD
23 | R14 | 0Ω | Vishay | WSL060300000ZEA9 | SMD Current Sense Resistor, Jumper, 0 ohm, WSL-9 Jumper, 0603 [1608 Metric], Metal Strip | 0603[1608 Metric] | SMD
24 | U1 | ATMEGA328P | Atmel | ATMEGA328P-PU | ATmega Series 20 MHz 32 KB Flash 2 KB SRAM 8-Bit Microcontroller | _ | THT
25 | U2 | DRA818V | Dorgi | DRA818V | VHF Band Voice Transceiver | _ | _
26 | U3 | DRA818U | Dorgi | DRA818U | UHF Band Voice Transceiver | _ | _
27 | U4 | LM2575S-3.3 | Texas Industries | LM2575S-3..3V | Buck (Step Down) Switching Regulator, Fixed, 4V-60V In, 3.3V And 2A Out, 52 kHz, TO-263-5 | _ | SMD
28 | J1 | DB9 Connector | TE Connectivity | M24308/23-25F | D-Sub MIL Spec Connectors R/A RCP ASSY 9 POS SER 109 | _ | THT
29 | J2 | Female Header | Local Vendor | _ | Local Vendor | 28 Pins | THT
30 | J3 | Female Header | Local Vendor | _ | Local Vendor | 2 Pins | THT
31 | J4 | Female Header | Local Vendor | _ | Local Vendor | 2 Pins | THT
32 | D1,D2 | Diode | DIODES INC. | DIODES INC. 1N5819HW-7-F | Schottky Rectifier, 40 V, 1 A, Single, SOD-123, 2 Pins, 750 mV | _ | SMD
33 | S1 | SMA Connector | LPRS | SMA RA CONNECTOR | RF / Coaxial Connector, SMA Coaxial, Solder | _ | THT
34 | Q1 | 8 Mhz | Oscillator | Crystal Oscillator | Crystal Oscillator 16 Mhz | _ | THT
35 | T1 | Microchip | 2N7000-G | MOSFET | Power MOSFET, N Channel, 60 V, 200 mA, 5 ohm, TO-92, Through Hole | _ | THT
36 | T2,T3 | Thermistor | NTC-100K | Thermistor NTC-100K | Thermistor 100k NTC with 1 Meter Cable Temperature Sensor | _ | THT
37 | F1 | Fuse | LITTEFUSE | 0448002.MR. | FUSE, SMD, 2A, FAST ACTING | _ | SMD

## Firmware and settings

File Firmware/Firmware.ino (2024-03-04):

/*
This firmware file is completed with credits to GitHUb user markqvist for their reposatory titled LibAPRS: https://github.com/markqvist/LibAPRS.git
It is recommended to look at their example code before trying to understand this firmware.

Date of updation: 04/03/2024
*/


#include <EEPROM.h>
#include "LibAPRS.h"
#include <SoftwareSerial.h>
#include <avr/wdt.h>

#define ADC_REFERENCE REF_3V3
#define OPEN_SQUELCH false
#define debug

#define SATCALL_SIGN "VU3CDI"   
#define GSCALL_SIGN "VU3OIR"
#define SATTELEM_SSID 11
#define SATDIGI_SSID 6
#define GS_SSID 1             


#define APRS_TOCALL "APUVU1"

#define PTT_VHF (3)           
#define UHF_POWER_DOWN_PIN (2)
#define UHF_RX (10)
#define UHF_TX (11)
#define VHF_RX (12)
#define VHF_TX (13)
#define THERM_1 (24)
#define THERM_2 (25)

//String VHF_SETUP_STRING = "AT+DMOSETGROUP=0,145.8250,145.8250,0000,0,0000\r\n";    //default values
#define UHF_SETUP_STRING "AT+DMOSETGROUP=0,437.0000,437.0000,0001,2,0001\r\n"        //default
#define TURN_OFF_VOICE_REPEATER digitalWrite(UHF_POWER_DOWN_PIN, LOW)   
#define TURN_ON_VOICE_REPEATER                                                 \
  do {                                                                         \
    digitalWrite(UHF_POWER_DOWN_PIN, HIGH);                                    \
    uhf_port.write(F(UHF_SETUP_STRING));                                       \                                 
  } while (0)

#define TOTAL_RESETS_EEPROM_ADDR 0x00
#define WD_INDUCED_RESETS_EEPROM_ADDR 0x02
#define TX_STATUS 0x04
#define Rx_Frequency 0x06 //need to check
#define Tx_Frequency 0x15 //need to check
char Rx_freq[8]="145.9800";
char Tx_freq[8]="145.9800";

#define COMMAND_INDICATOR '!'

SoftwareSerial vhf_port(VHF_RX, VHF_TX);
SoftwareSerial uhf_port(UHF_RX, UHF_TX);

int TELEMETRY_INTERVAL= 30000; // milliseconds
boolean gotPacket = false;
AX25Msg incomingPacket;
uint8_t *packetData;

boolean digipeater_is_on = false;
boolean voice_repeater_is_on = false;
boolean transmission_is_on;
uint16_t total_resets;
uint16_t wd_induced_resets ;
long last_telemetry_time;


void watchdogSetup(void) {
  cli();
  wdt_reset();
  WDTCSR |= (1 << WDCE) | (1 << WDE);
  WDTCSR = (1 << WDIE) | (1 << WDE) | (1 << WDP3) | (0 << WDP2) | (0 << WDP1) |
           (1 << WDP0);
  sei();
}

// This function is to copy the received and decoded packet into the controller's memory.
void aprs_msg_callback(struct AX25Msg *msg) {
  if (!gotPacket) {
    gotPacket = true;
    memcpy(&incomingPacket, msg, sizeof(AX25Msg));
    if (freeMemory() > msg->len) {
      packetData = (uint8_t *)malloc(msg->len);
      memcpy(packetData, msg->info, msg->len);
      incomingPacket.info = packetData;
    } else {
      gotPacket = false;
    }
  }
}


ISR(WDT_vect) {
  wd_induced_resets++;  // Increment the watchdog-induced resets variable
  EEPROM.write(WD_INDUCED_RESETS_EEPROM_ADDR, wd_induced_resets);   // Store the updated value in the permanent memory of the controller
}

void setup() {
#ifdef debug
  Serial.begin(9600);
#endif

  watchdogSetup();
  EEPROM.get(TOTAL_RESETS_EEPROM_ADDR, total_resets);

  // Increment the value of 'total_resets' and store it at memory address 0x00
  total_resets++;   
  EEPROM.put(TOTAL_RESETS_EEPROM_ADDR, total_resets);
  EEPROM.get(WD_INDUCED_RESETS_EEPROM_ADDR, wd_induced_resets);
  EEPROM.get(TX_STATUS, transmission_is_on);

  //pinMode(UHF_POWER_DOWN_PIN, OUTPUT);
  //digitalWrite(UHF_POWER_DOWN_PIN,LOW);        //turn DRA818U off

  vhf_port.begin(9600);
  uhf_port.begin(9600);

  EEPROM.get(Rx_Frequency,Rx_freq);
  EEPROM.get(Tx_Frequency,Tx_freq);
  
  DRA_V_config(Rx_freq,Tx_freq);

  wdt_reset();

  APRS_init(ADC_REFERENCE, OPEN_SQUELCH);
  APRS_setCallsign(SATCALL_SIGN, SATTELEM_SSID);
  APRS_setDestination(APRS_TOCALL, 0);

  APRS_setPreamble(350);
  APRS_setTail(100);

#ifdef debug
  APRS_printSettings();
  Serial.print(F("Free RAM:     "));
  Serial.println(freeMemory());
#endif

  last_telemetry_time = millis();
}

void loop() {
  processPacket();
  #ifdef debug
  Serial.println(wd_induced_resets);
  #endif
  
  if (millis() - last_telemetry_time >= TELEMETRY_INTERVAL && transmission_is_on){
    send_telemetry();
  }
  wdt_reset();
}


void processPacket() {
  if (gotPacket) {
    gotPacket = false;

    #ifdef debug
      Serial.print(F("Received APRS packet. SRC: "));
      Serial.print(incomingPacket.src.call);
      Serial.print(F("-"));
      Serial.print(incomingPacket.src.ssid);
      Serial.print(F(". DST: "));
      Serial.print(incomingPacket.dst.call);
      Serial.print(F("-"));
      Serial.print(incomingPacket.dst.ssid);
      Serial.print(F(". Data: "));

      for (int i = 0; i < incomingPacket.len; i++) {
        Serial.write(incomingPacket.info[i]);
      }
      Serial.println("");
    #endif

   if(recieve_command()){
    switch (incomingPacket.info[1]){              //@ for changing modes, # for changing RX freq, % for changing TX freq
      case '@':{
            switch(incomingPacket.info[2]){
                case '0': {
                  TURN_OFF_VOICE_REPEATER;
                  voice_repeater_is_on=false;
                  TELEMETRY_INTERVAL=30000;
                  break;
                }
                case '1':{
                  TURN_OFF_VOICE_REPEATER;
                  voice_repeater_is_on=false;
                  TELEMETRY_INTERVAL=60000;
                  break;
                }
                case '2':{
                  TURN_ON_VOICE_REPEATER;
                  TELEMETRY_INTERVAL=60000;
                  voice_repeater_is_on=true;
                  break;
                }
                default:{                            //default being go back to safe mode
                  TURN_OFF_VOICE_REPEATER;
                  voice_repeater_is_on=false;
                  TELEMETRY_INTERVAL=30000;
                  break;
                }
        }
        break;
      }
      
      case '#':{
        for(int i=0;i<8;i++){
          Rx_freq[i]=incomingPacket.info[(3+i)];
        }
        EEPROM.put(Rx_Frequency,Rx_freq);
        DRA_V_config(Rx_freq,Tx_freq);
        break;
      }
      
      case '%':{
        for(int i=0;i<8;i++){
          Tx_freq[i]=incomingPacket.info[(3+i)];
        }
        EEPROM.put(Tx_Frequency,Tx_freq);
        DRA_V_config(Rx_freq,Tx_freq);
        break;
      }
    }
    
   // If not a command: Check digipeater/transmission, set 'do_repeat' if needed.
   } else {
        boolean do_repeat = false;
        for (int i = 0; i < incomingPacket.rpt_count; i++) {
          if (!strcmp(incomingPacket.rpt_list[i].call, "ARISS") ||
              !strcmp(incomingPacket.rpt_list[i].call, SATCALL_SIGN)) {
            do_repeat = true;
          }
        }
        if (do_repeat) {
          APRS_setCallsign(incomingPacket.src.call, incomingPacket.src.ssid);
          APRS_setPath1(SATCALL_SIGN, (SATDIGI_SSID | 0x40));
          APRS_sendPkt(&incomingPacket.info[0], incomingPacket.len);
          APRS_setCallsign(SATCALL_SIGN, SATTELEM_SSID);  // Reset Callsign and Path1 values after sending the packet.
          APRS_setPath1("WIDE1", 1);
        }
      
      free(packetData); // Free the packetdata to make space in memory for next packet
    }
   
  }

}

bool recieve_command(){
  // This if statement verifies if the received packet is a command for the satellite.
  if( incomingPacket.src.call == SATCALL_SIGN &&
      incomingPacket.src.ssid == GS_SSID &&
      incomingPacket.info[0] == COMMAND_INDICATOR &&
      incomingPacket.dst.call == SATCALL_SIGN &&
      incomingPacket.dst.ssid == SATTELEM_SSID){
          return true;
  }
  else{
    return false;
  }
}


float get_Temperature(int thermistor_output){
  int thermistor_adc_val;
  float output_voltage, thermistor_resistance, therm_res_ln, temperature; 
  thermistor_adc_val = analogRead(thermistor_output);

  ADMUX = 0;
  output_voltage = ( (thermistor_adc_val * 3.3) / 1023.0 );
  thermistor_resistance = ( ( 3.3 * ( 10.0 / output_voltage ) ) - 10 ); /* Resistance in kilo ohms */
  thermistor_resistance = thermistor_resistance * 1000 ; /* Resistance in ohms   */
  therm_res_ln = log(thermistor_resistance);
  temperature = ( 1 / ( 0.001129148 + ( 0.000234125 * therm_res_ln ) + ( 0.0000000876741 * therm_res_ln * therm_res_ln * therm_res_ln ) ) ); /* Temperature in Kelvin */
  temperature = temperature - 273.15;
  #ifdef debug
    Serial.print("Temperature in degree Celsius = ");
    Serial.print(temperature);
    Serial.print("\t\t");
    Serial.print("Resistance in ohms = ");
    Serial.print(thermistor_resistance);
    Serial.print("\n\n");
  #endif
  return temperature ;
}

void send_telemetry(){
  //APRS_setMessageDestination("NOCALL", 0);          //for testing
  wdt_reset();
  float float_temp1=  get_Temperature(THERM_1);       
  float float_temp2=  get_Temperature(THERM_2);

  String temp1= String(float_temp1);
  String temp2= String(float_temp2);
  String watchdog_resets_no= String(wd_induced_resets);

  EEPROM.get(TOTAL_RESETS_EEPROM_ADDR, total_resets);
  uint8_t total_resets_lsb = (total_resets & 0x00FF);
  uint8_t total_resets_msb = ((total_resets & 0xFF00) >>8);
  String sss = String(total_resets_lsb);
  String resets_msb = String(total_resets_msb);
  EEPROM.get(WD_INDUCED_RESETS_EEPROM_ADDR, wd_induced_resets);  // Get total number of resets from memory
  uint8_t wd_induced_resets_lsb = (wd_induced_resets & 0x00FF);  // Separate 16-bit integer into two 8-bit integers (LSB and MSB)
  uint8_t wd_induced_resets_msb = ((wd_induced_resets & 0xFF00) >>8);
  String wd_lsb = String(wd_induced_resets_lsb);  // Convert total resets to strings
  String wd_msb = String(wd_induced_resets_msb);

  // Concat all the statuses and sensor values into one long string
  String telemetry = "t#" + sss + "," + resets_msb + "," + wd_lsb + "," + wd_msb + "," + temp1 + "," + temp2 + ","+ "xxxxxx" +  "BeliefSat-0";
  // Convert the string into a character array
  char message[telemetry.length()] = "";     
  telemetry.toCharArray(message, telemetry.length());
  
  APRS_sendMsg(message, strlen(message));   //Send telemetry as a mesage.
  
  last_telemetry_time = millis();
  
}


//Function for setting DRA818V frequency
void DRA_V_config(String Rx_freq, String Tx_freq) {
  vhf_port.begin(9600);
  // Set DRA818V frequency
  String cmd=("AT+DMOSETGROUP=0," + Rx_freq + "," + Tx_freq + ",0002,1,0002\r\n");
  //Serial.println(cmd);    //For debugging
  vhf_port.write(cmd.c_str());
  delay(100); // Give some time to receive the acknowledgment
  #ifdef debug
  while (vhf_port.available()) {
    char response = vhf_port.read();
    Serial.write(response); // Print the acknowledgment response on the Serial monitor
  #endif
}
}

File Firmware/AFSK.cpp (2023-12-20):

#include <string.h>
#include "AFSK.h"
#include "Arduino.h"

extern unsigned long custom_preamble;
extern unsigned long custom_tail;
extern int LibAPRS_vref;
extern bool LibAPRS_open_squelch;

bool hw_afsk_dac_isr = false;
bool hw_5v_ref = false;
Afsk *AFSK_modem;


// Forward declerations
int afsk_getchar(void);
void afsk_putchar(char c);

void AFSK_hw_refDetect(void) {
    // This is manual for now
    if (LibAPRS_vref == REF_5V) {
        hw_5v_ref = true;
    } else {
        hw_5v_ref = false;
    }
}

void AFSK_hw_init(void) {
    // Set up ADC

    AFSK_hw_refDetect();

    TCCR1A = 0;                                    
    TCCR1B = _BV(CS10) | _BV(WGM13) | _BV(WGM12);
    ICR1 = (((CPU_FREQ+FREQUENCY_CORRECTION)) / 9600) - 1;

    if (hw_5v_ref) {
        ADMUX = _BV(REFS0) | 0;
    } else {
        ADMUX = 0;
    }

    ADC_DDR  &= ~_BV(0);
    ADC_PORT &= ~_BV(0);
    DIDR0 |= _BV(0);
    ADCSRB =    _BV(ADTS2) |
                _BV(ADTS1) |
                _BV(ADTS0);  
    ADCSRA =    _BV(ADEN) |
                _BV(ADSC) |
                _BV(ADATE)|
                _BV(ADIE) |
                _BV(ADPS2);

    AFSK_DAC_INIT();
   // LED_TX_INIT();
   // LED_RX_INIT();
}

void AFSK_init(Afsk *afsk) {
    // Allocate modem struct memory
    memset(afsk, 0, sizeof(*afsk));
    AFSK_modem = afsk;
    // Set phase increment
    afsk->phaseInc = MARK_INC;
    // Initialise FIFO buffers
    fifo_init(&afsk->delayFifo, (uint8_t *)afsk->delayBuf, sizeof(afsk->delayBuf));
    fifo_init(&afsk->rxFifo, afsk->rxBuf, sizeof(afsk->rxBuf));
    fifo_init(&afsk->txFifo, afsk->txBuf, sizeof(afsk->txBuf));

    // Fill delay FIFO with zeroes
    for (int i = 0; i<SAMPLESPERBIT / 2; i++) {
        fifo_push(&afsk->delayFifo, 0);
    }

    AFSK_hw_init();

}

static void AFSK_txStart(Afsk *afsk) {
    if (!afsk->sending) {
        afsk->phaseInc = MARK_INC;
        afsk->phaseAcc = 0;
        afsk->bitstuffCount = 0;
        afsk->sending = true;
       // LED_TX_ON();
        afsk->preambleLength = DIV_ROUND(custom_preamble * BITRATE, 8000);
        AFSK_DAC_IRQ_START();
    }
    ATOMIC_BLOCK(ATOMIC_RESTORESTATE) {
      afsk->tailLength = DIV_ROUND(custom_tail * BITRATE, 8000);
    }
}

void afsk_putchar(char c) {
    AFSK_txStart(AFSK_modem);
    while(fifo_isfull_locked(&AFSK_modem->txFifo)) { /* Wait */ }
    fifo_push_locked(&AFSK_modem->txFifo, c);
}

int afsk_getchar(void) {
    if (fifo_isempty_locked(&AFSK_modem->rxFifo)) {
        return EOF;
    } else {
        return fifo_pop_locked(&AFSK_modem->rxFifo);
    }
}

void AFSK_transmit(char *buffer, size_t size) {
    fifo_flush(&AFSK_modem->txFifo);
    int i = 0;
    while (size--) {
        afsk_putchar(buffer[i++]);
    }
}

uint8_t AFSK_dac_isr(Afsk *afsk) {
    if (afsk->sampleIndex == 0) {
        if (afsk->txBit == 0) {
            if (fifo_isempty(&afsk->txFifo) && afsk->tailLength == 0) {
                AFSK_DAC_IRQ_STOP();
                afsk->sending = false;
               // LED_TX_OFF();
                return 0;
            } else {
                if (!afsk->bitStuff) afsk->bitstuffCount = 0;
                afsk->bitStuff = true;
                if (afsk->preambleLength == 0) {
                    if (fifo_isempty(&afsk->txFifo)) {
                        afsk->tailLength--;
                        afsk->currentOutputByte = HDLC_FLAG;
                    } else {
                        afsk->currentOutputByte = fifo_pop(&afsk->txFifo);
                    }
                } else {
                    afsk->preambleLength--;
                    afsk->currentOutputByte = HDLC_FLAG;
                }
                if (afsk->currentOutputByte == AX25_ESC) {
                    if (fifo_isempty(&afsk->txFifo)) {
                        AFSK_DAC_IRQ_STOP();
                        afsk->sending = false;
                       // LED_TX_OFF();
                        return 0;
                    } else {
                        afsk->currentOutputByte = fifo_pop(&afsk->txFifo);
                    }
                } else if (afsk->currentOutputByte == HDLC_FLAG || afsk->currentOutputByte == HDLC_RESET) {
                    afsk->bitStuff = false;
                }
            }
            afsk->txBit = 0x01;
        }

        if (afsk->bitStuff && afsk->bitstuffCount >= BIT_STUFF_LEN) {
            afsk->bitstuffCount = 0;
            afsk->phaseInc = SWITCH_TONE(afsk->phaseInc);
        } else {
            if (afsk->currentOutputByte & afsk->txBit) {
                afsk->bitstuffCount++;
            } else {
                afsk->bitstuffCount = 0;
                afsk->phaseInc = SWITCH_TONE(afsk->phaseInc);
            }
            afsk->txBit <<= 1;
        }

        afsk->sampleIndex = SAMPLESPERBIT;
    }

    afsk->phaseAcc += afsk->phaseInc;
    afsk->phaseAcc %= SIN_LEN;
    afsk->sampleIndex--;

    return sinSample(afsk->phaseAcc);
}
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
